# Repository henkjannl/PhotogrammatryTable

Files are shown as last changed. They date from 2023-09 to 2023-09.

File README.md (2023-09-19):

# PhotogrammatryTable

This is a design of a rotary table that can be used to 3D scan objects.

The turntable consists of a 3D printable housing, a stepper motor with stepper motor driver, an ESP32.

It can be controlled by a serial connection, but also wireless by an M5Stack, if you have one available.

| Item | Number | Description | Type | Link |
|:----:|:---:|---|---|---|
| 1  | 1 | Bottom housing | 3D printable | Rotary table btm.stl |
| 2  | 1 | Top housing | 3D printable | Rotary table top.stl |
| 3  | 1 | Rotary table | 3D printable | Rotary table.stl |
| 4  | 1 | Stepper motor | 28BYJ-48 | |
| 5  | 1 | Stepper driver board  | ULN2003 | |
| 6  | 1 | Microcontroller | ESP32-mh-et-live-minikit-d1 | |
| 7  | 3 | Self tapping screws | M2.6 x 16 | |
| 8  | 1 | M5 Stack (optional) | | |

The STL files for 3D printing are in the mechanical directory. The design was made in FreeCAD, FreeCAD files are included. 

Electrical connections (only 6 wires) are in the mechanical directory.

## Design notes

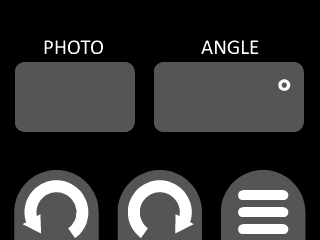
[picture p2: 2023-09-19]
04 User interface/main_screen.png

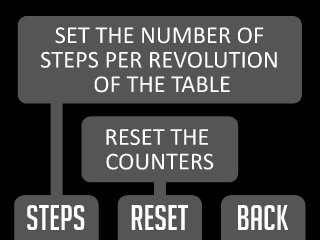
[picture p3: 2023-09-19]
04 User interface/settings_screen.png

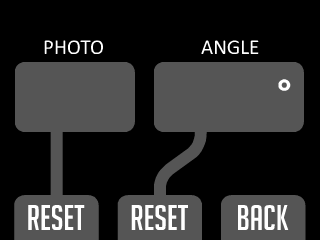
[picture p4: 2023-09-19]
04 User interface/reset_screen.png

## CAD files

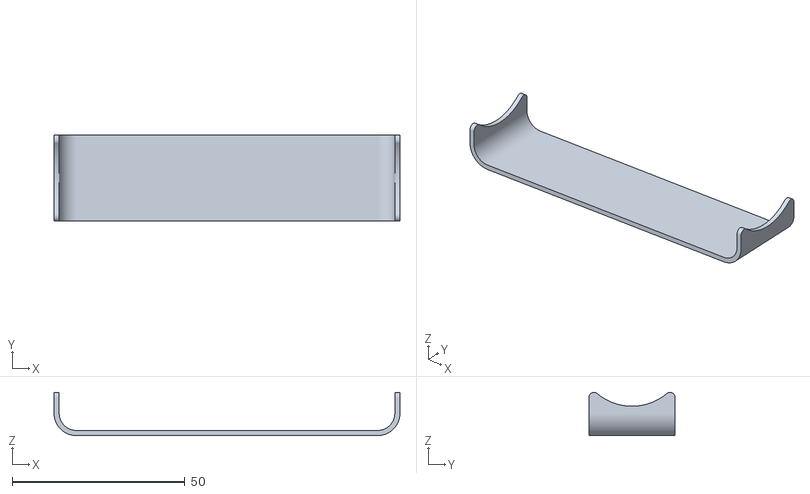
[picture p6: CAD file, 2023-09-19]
01 Mechanical/houder zonnebril henkjan 1.stl
100.0 x 25.0 x 12.5

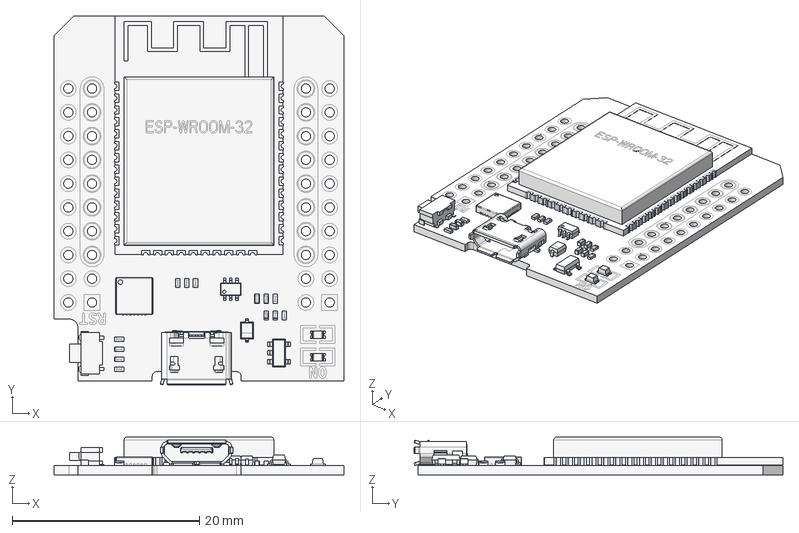
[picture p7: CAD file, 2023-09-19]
01 Mechanical/Components/ESP32-mh-et-live-minikit-d1.FCStd
31.0 x 39.4 x 4.04 mm

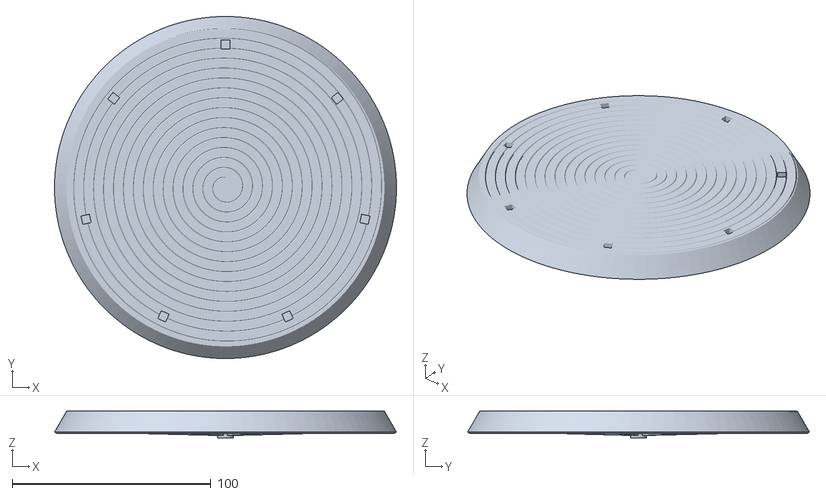
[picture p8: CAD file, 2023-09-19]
01 Mechanical/Flat rotary table.stl
172.2 x 172.2 x 13.5

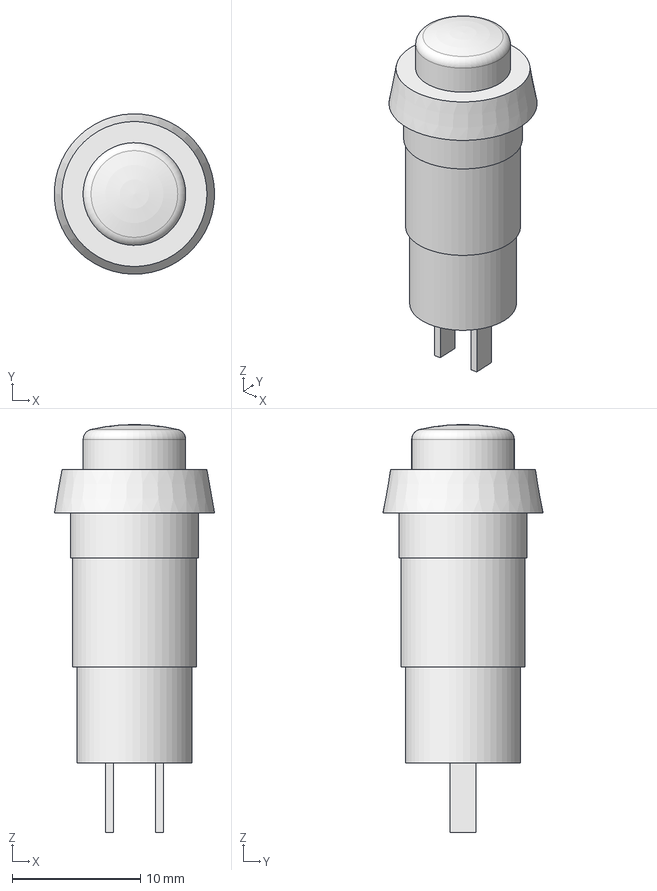
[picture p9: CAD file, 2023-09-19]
01 Mechanical/Components/Pushbutton.FCStd
12.5 x 12.5 x 31.8 mm

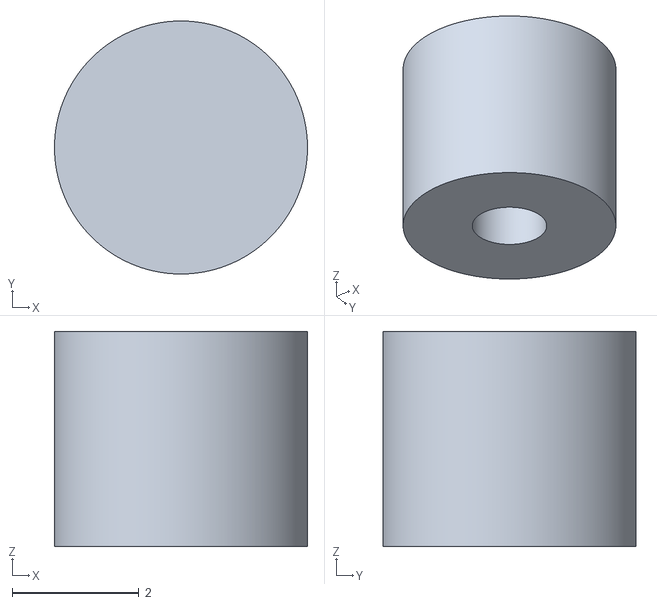
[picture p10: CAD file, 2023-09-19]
01 Mechanical/Endstop.stl
4.00 x 4.00 x 3.40

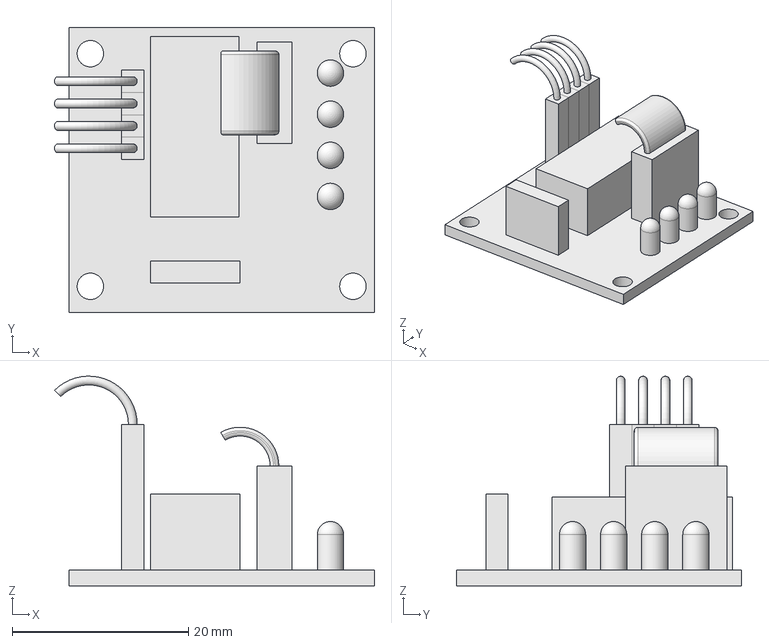
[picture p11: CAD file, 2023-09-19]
01 Mechanical/Components/ULN2003 stepper driver board.FCStd
36.3 x 32.3 x 23.8 mm

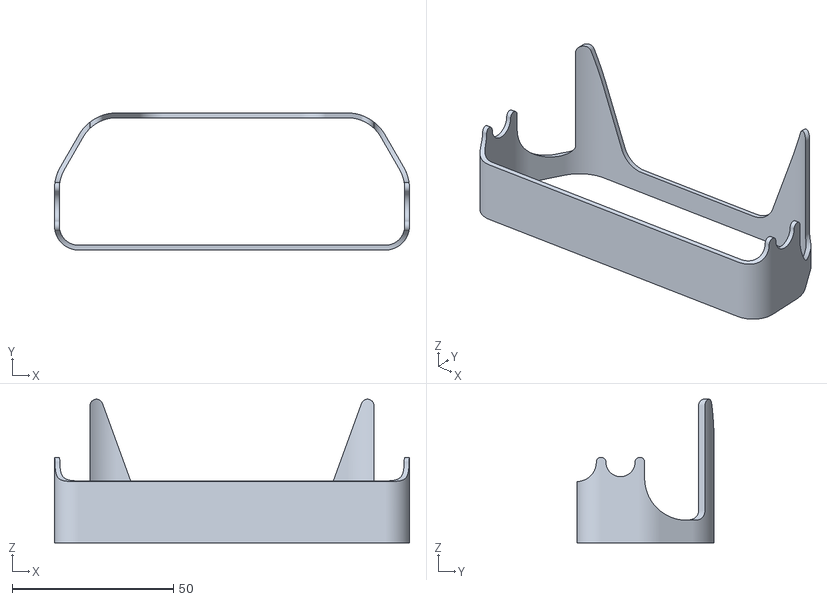
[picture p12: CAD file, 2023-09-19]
01 Mechanical/houder zonnebril henkjan 2.stl
110.0 x 42.5 x 44.5

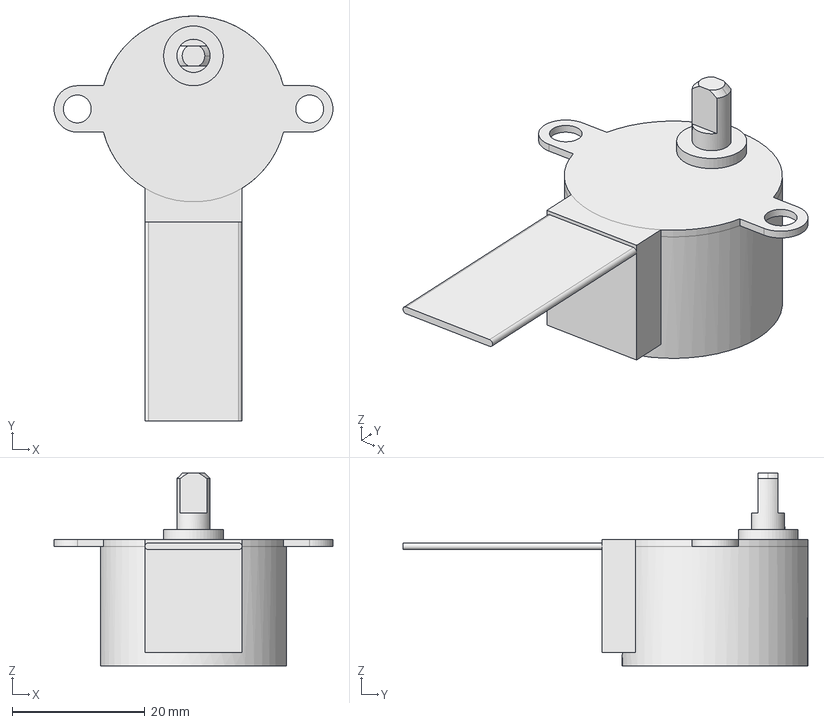
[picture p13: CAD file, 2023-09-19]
01 Mechanical/Components/28BYJ-48 stepper motor.FCStd
42.0 x 61.0 x 29.0 mm

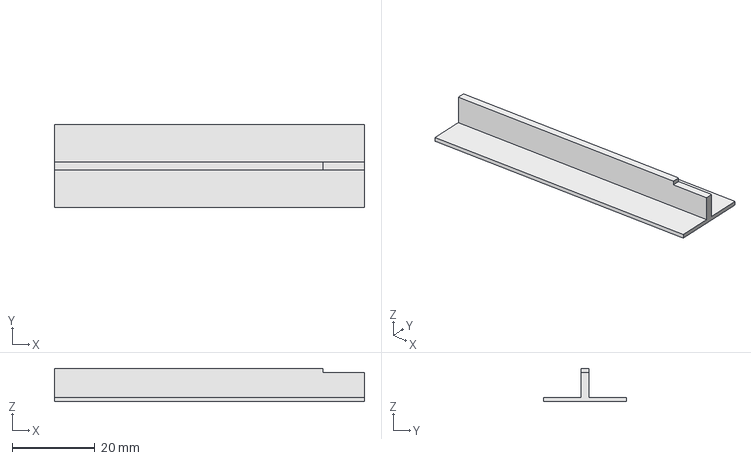
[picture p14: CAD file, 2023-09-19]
01 Mechanical/FEM analysis.FCStd
75.0 x 20.0 x 8.00 mm

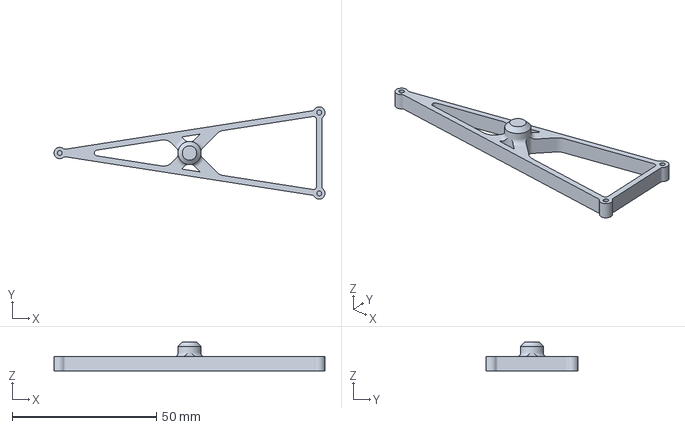
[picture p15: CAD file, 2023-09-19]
01 Mechanical/Adaptor.3mf
94.0 x 32.0 x 10.0 mm

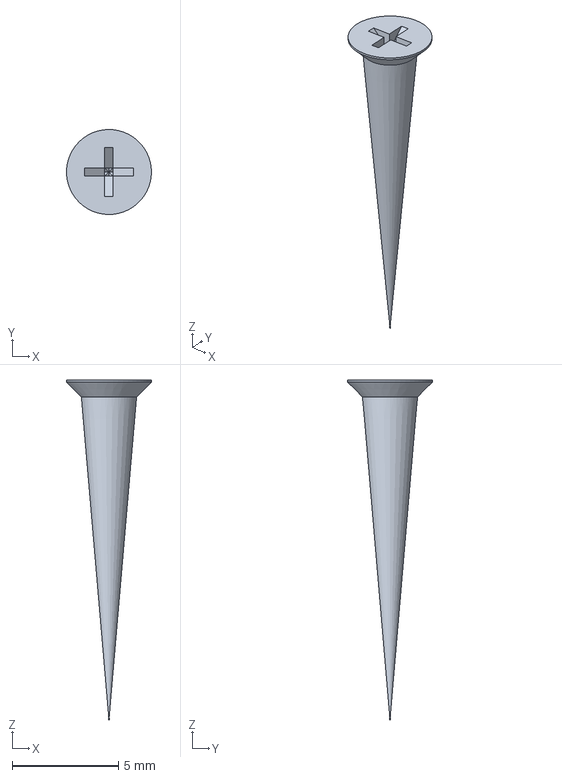
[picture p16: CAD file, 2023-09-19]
01 Mechanical/Components/SelftappingScrew2.6x16.FCStd
4.00 x 4.00 x 16.0 mm

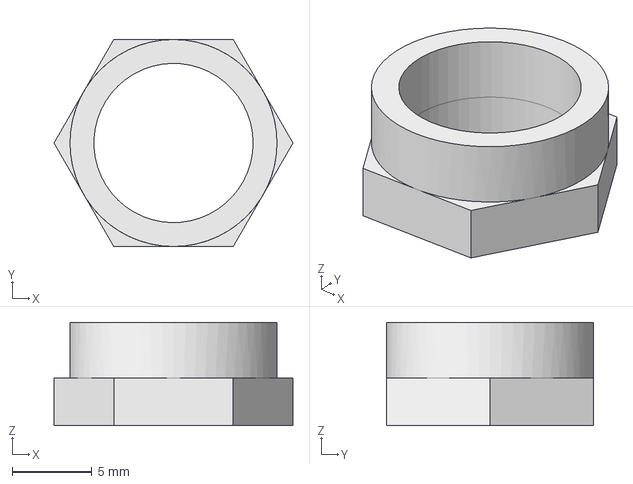
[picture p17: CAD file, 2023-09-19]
01 Mechanical/Components/Pushbutton-nut.FCStd
15.0 x 13.0 x 6.50 mm

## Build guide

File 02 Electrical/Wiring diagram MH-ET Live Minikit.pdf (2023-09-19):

BOTTOM VIEW MH-ET LIVE MINIKIT ConneconGPIO

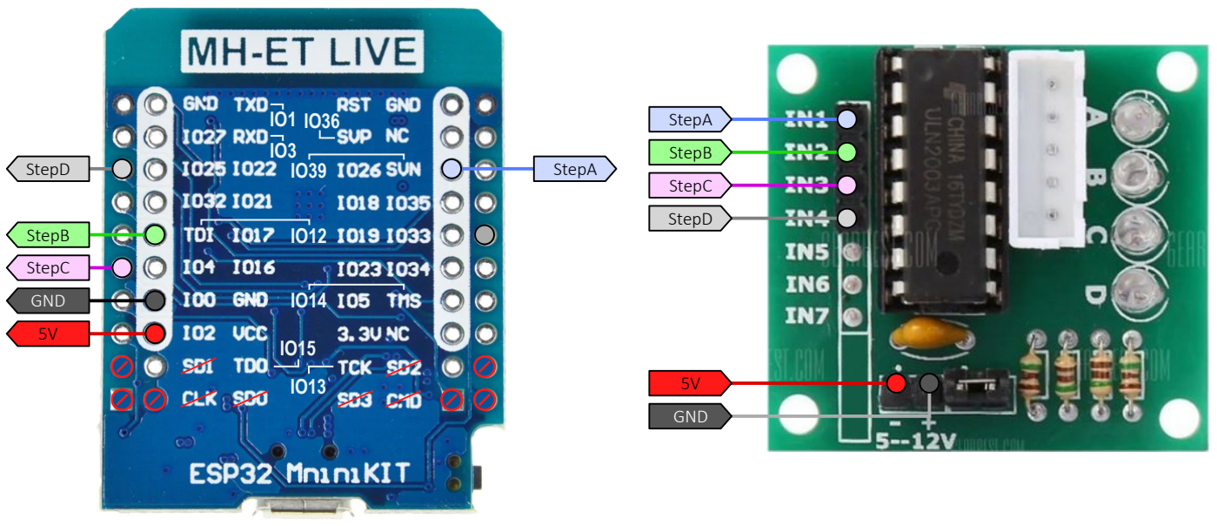
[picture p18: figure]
StepA; StepB; StepC; StepD; GND

4 StepC
25 StepD

17 StepB

26 StepA

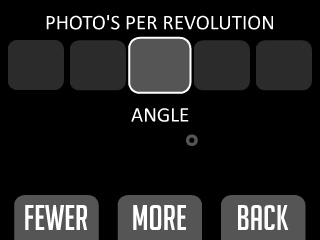
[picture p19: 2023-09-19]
04 User interface/steps_screen.png

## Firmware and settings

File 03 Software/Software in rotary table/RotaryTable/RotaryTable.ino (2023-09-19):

#include "WiFi.h"
#include <esp_now.h>
#include "Stepper.h"

#define STEPS_PER_REV  4096
#define DEBUG true

// mac address of the remote controller
const uint8_t broadcastAddress[] = {0xB4, 0xE6, 0x2D, 0xFB, 0x05, 0x11};

enum comm_state_t { cmsIdle, cmsRequestFromRemote, cmsError };

// == GLOBAL VARIABLES ==
// Variables for serial control
int inByte = 0;        // incoming serial byte
int NumberReceived = 0;
int counter = 1;

esp_now_peer_info_t peerInfo;
comm_state_t comm_state = cmsIdle;

// Variables for the stepper motor
Stepper table = Stepper(26, 17, 4, 25);
int stepsPerMove = STEPS_PER_REV / 35;

// == ESP-NOW interface ==
enum message_type_t { msgRequestTurn, msgAcknowledge, msgMotionCompleted, msgError };

struct message_t {
  message_type_t message_type;
  float angle;
};

void send_message(message_type_t message_type ) {

  // Prepare message for remote controller
  message_t message = { message_type, 0 };

  // Send message to remote controller
  esp_err_t result = esp_now_send(broadcastAddress, (uint8_t *) &message, sizeof(message));

  if(result==ESP_NOW_SEND_FAIL) {
    comm_state = cmsError;
  }
};

//typedef void (*esp_now_send_cb_t)(const uint8_t *mac_addr, esp_now_send_status_t status)
void send_callback(const uint8_t *mac_addr, esp_now_send_status_t status) {
  if(status!=ESP_NOW_SEND_SUCCESS) {
    comm_state = cmsError;
  }
};

//typedef void (*esp_now_recv_cb_t)(const esp_now_recv_info_t *esp_now_info, const uint8_t *data, int data_len)
void receive_callback(const uint8_t * mac, const uint8_t *data, int len) {
  message_t message;
  memcpy(&message, data, sizeof(message_t) );

  // Confirm message was received
  send_message(msgAcknowledge);

  int stepsPerMove = STEPS_PER_REV * message.angle / 360;
  table.moveRelative( 1000, stepsPerMove );   

  comm_state = cmsRequestFromRemote;
}

void setup() {

  // Initialize serial interface
  Serial.begin(115200);
  while (!Serial) {
    ;  // wait for serial port to connect. Needed for native USB port only
  }

  WiFi.mode(WIFI_MODE_STA);
  if (esp_now_init() != ESP_OK) Serial.println("Error initializing ESP-NOW");

  // Register peer
  memcpy(peerInfo.peer_addr, broadcastAddress, 6);
  peerInfo.channel = 0;  
  peerInfo.encrypt = false;
  
  if (esp_now_add_peer(&peerInfo) != ESP_OK){
    Serial.println("Failed to add peer");
    return;
  }

  // Setup callback function for ESP-NOW
  esp_now_register_recv_cb(receive_callback);
  esp_now_register_send_cb(send_callback);

  // Initialize stepper motor
  table.moveRelative( 10000, STEPS_PER_REV );   
  while(table.moving) {
    table.run();
  }

  #if DEBUG
    Serial.println(WiFi.macAddress());
  #endif

  Serial.println("Rotary table initialized");
}

void loop() {
  if (Serial.available() > 0) {
    // get incoming byte:
    inByte = Serial.read();

    /*    Character	ASCII
          \n         10
          \r         13
          R          82
          r         114
          ,          44
          <          60
          .          46
          >          62
          0          48
          :          :
          9          57        */

    if( ( inByte == 82 ) || ( inByte == 114 ) ) {
      // 'r' or 'R' reset the counter
      counter = 1;
      Serial.printf("Counter reset to %d\n", counter);
    }

    else if( ( inByte == 44 ) || ( inByte == 60 ) ) {
      // '<' or ',' make the table run counter clockwise
      Serial.printf("Photo %d. Table moving CCW %d steps\n", counter, stepsPerMove);
      table.moveRelative( 1000, -stepsPerMove );   
      NumberReceived=0;
      counter++;
    } // ( inByte == 44 ) || ( inByte == 60 )

    else if( ( inByte == 46 ) || ( inByte == 62 ) ) {
      // '>' or '.' make the table run clockwise
      Serial.printf("Photo %d. Table moving CW %d steps\n", counter, stepsPerMove);
      table.moveRelative( 1000, stepsPerMove );   
      NumberReceived=0;
      counter++;
    } // ( inByte == 46 ) || ( inByte == 62 )

    else if( ( inByte == 10 ) || ( inByte == 13 ) ) {
      // CR or LF enter the new number
      if( (NumberReceived>0) && (NumberReceived<STEPS_PER_REV) ) {
        stepsPerMove = (int) (STEPS_PER_REV / NumberReceived + 0.5);
        Serial.printf("Number of stops per revolution: %d. Steps per move: %d\n", NumberReceived, stepsPerMove );
      } // NumberReceived>0
      NumberReceived=0;
    } // ( inByte == 13 )

    else if( ( inByte >= 48 ) && ( inByte <= 57 ) ) {
      // 0..9 add something to the number being entered
      NumberReceived = 10*NumberReceived + (inByte-48);
    }  // ( inByte >= 48 ) && ( inByte <= 57 ) )

  } // Serial.available() > 0 

  // Run the table
  table.run();

  // Report that the move is completed
  if ( (comm_state==cmsRequestFromRemote) and (not table.moving) ) {
    comm_state = cmsIdle;
    send_message(msgMotionCompleted);
  }

} // loop() 

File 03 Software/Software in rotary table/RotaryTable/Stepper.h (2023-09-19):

//====================================================================================
//                                         Stepper
//====================================================================================

class Stepper {
  public:
    uint8_t pin1, pin2, pin3, pin4;
    bool moving;
    unsigned long originTime, duration;
    int originPos, currentPos, targetPos;

    Stepper( int pin1, int pin2, int pin3, int pin4 );
    void move( unsigned long duration, int target);
    void moveRelative( unsigned long duration, int stroke);
    void setOutputs();
    void idle();
    void run();
} ;

Stepper::Stepper( int pin1, int pin2, int pin3, int pin4 ) {
  
  this->pin1 = pin1;
  this->pin2 = pin2;
  this->pin3 = pin3;
  this->pin4 = pin4;
  
  this->moving=false;
  this->currentPos=0;

  pinMode(pin1, OUTPUT);
  pinMode(pin2, OUTPUT);
  pinMode(pin3, OUTPUT);
  pinMode(pin4, OUTPUT);
};

void Stepper::move( unsigned long duration, int target) {
  moving=true;
  originTime=millis();
  this->duration=duration;
  originPos=currentPos;
  targetPos=target;
}

void Stepper::moveRelative( unsigned long duration, int stroke) {
  moving=true;
  originTime=millis();
  this->duration=duration;
  originPos=currentPos;
  targetPos+=stroke;
}

void Stepper::setOutputs() {

  int state = currentPos % 8;
  if(state<0) state+=8;
  
  switch (state) {
    case 0:
      digitalWrite(pin1, HIGH);
      digitalWrite(pin2, LOW );
      digitalWrite(pin3, LOW );
      digitalWrite(pin4, LOW );
      break;

    case 1:
      digitalWrite( pin1, HIGH );
      digitalWrite( pin2, HIGH );
      digitalWrite( pin3, LOW  );
      digitalWrite( pin4, LOW  );
      break;

    case 2:
      digitalWrite( pin1, LOW  );
      digitalWrite( pin2, HIGH );
      digitalWrite( pin3, LOW  );
      digitalWrite( pin4, LOW  );
      break;

    case 3:
      digitalWrite( pin1, LOW  );
      digitalWrite( pin2, HIGH );
      digitalWrite( pin3, HIGH );
      digitalWrite( pin4, LOW  );
      break;

    case 4:
      digitalWrite( pin1, LOW  );
      digitalWrite( pin2, LOW  );
      digitalWrite( pin3, HIGH );
      digitalWrite( pin4, LOW  );
      break;

    case 5:
      digitalWrite( pin1, LOW  );
      digitalWrite( pin2, LOW  );
      digitalWrite( pin3, HIGH );
      digitalWrite( pin4, HIGH );
      break;

    case 6:
      digitalWrite( pin1, LOW  );
      digitalWrite( pin2, LOW  );
      digitalWrite( pin3, LOW  );
      digitalWrite( pin4, HIGH );
      break;

    case 7:
      digitalWrite( pin1, HIGH );
      digitalWrite( pin2, LOW  );
      digitalWrite( pin3, LOW  );
      digitalWrite( pin4, HIGH );
      break;
  }
  
  // Give the motor some time to respond
  delayMicroseconds(600);
}

void Stepper::idle() {
  moving=false;
  digitalWrite( pin1, LOW );
  digitalWrite( pin2, LOW );
  digitalWrite( pin3, LOW );
  digitalWrite( pin4, LOW );
}

void Stepper::run() {

  // Directly go back if the stepper state is idle
  if (!moving) return;
  
  // Calculate where we are in time and place
  float relTime = (float) ( millis() - originTime ) / duration;

  if (relTime>=1) relTime=1;

  float relPos = -4.311125*pow(relTime,5)+10.77781*pow(relTime,4)-11.18382*pow(relTime,3)+5.997917*pow(relTime,2)-0.28631*relTime+0.0027674;
  int desiredPos = (int) originPos+( targetPos-originPos ) * relPos + 0.5;

  // Move the stepper backward or forward
  if( desiredPos > currentPos ) {
    // Stepper needs to move forward
    while( desiredPos> currentPos ) {
      currentPos++;
      setOutputs();
    }
  }
  else {
    // Stepper needs to move backward
    while( desiredPos < currentPos) {
      currentPos--;
      setOutputs();
    }
  }

  // Switch off the motor to preserve power
  if ( millis() - originTime > duration ) {
    idle();
  }
}
